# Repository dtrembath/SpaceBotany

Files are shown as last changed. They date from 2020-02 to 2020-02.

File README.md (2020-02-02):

# SpaceBotany
Details of aeroponic mister control using esp8266

This is supplementary material for the Amateur Professionals team entry in the Grow Beyond Earth contest (Feb 3, 2020). 
The design uses a 113kHz piezoelectric mister w/ WG3166A board to aeroponically grow lettuce plants.
See https://www.instructables.com/contest/beyondEarth/ for details.

Files in this repository inlude 'mister-esp8266-wiring.pdf', which shows the wiring for controlling the mister with an ESP8266 microcontroller. A DHT22 temp/humidity sensor is also included. 
Data is uploaded to https://thingspeak.com/channels/948030

The Arduino IDE is used to upload the 'space_botany_contest_mister.ino' code to an Adafruit Feather Huzzah ESP 8266.
You will also need to download the 'secrets.h' file into the same directory as 'space_botany_contest_mister.ino'.
Edit the information in 'secrets.h' to add your wifi and ThingSpeak credentials.

The 'esp8266-mister.fzz' file is included if you'd like to open it with the Fritzing software tool.

See https://learn.adafruit.com/adafruit-feather-huzzah-esp8266/power-management for various ways to provide power to the ESP8266.
The WG3166A mister board draws a fair amount of current, so it has its own 5v 1.5A power supply.

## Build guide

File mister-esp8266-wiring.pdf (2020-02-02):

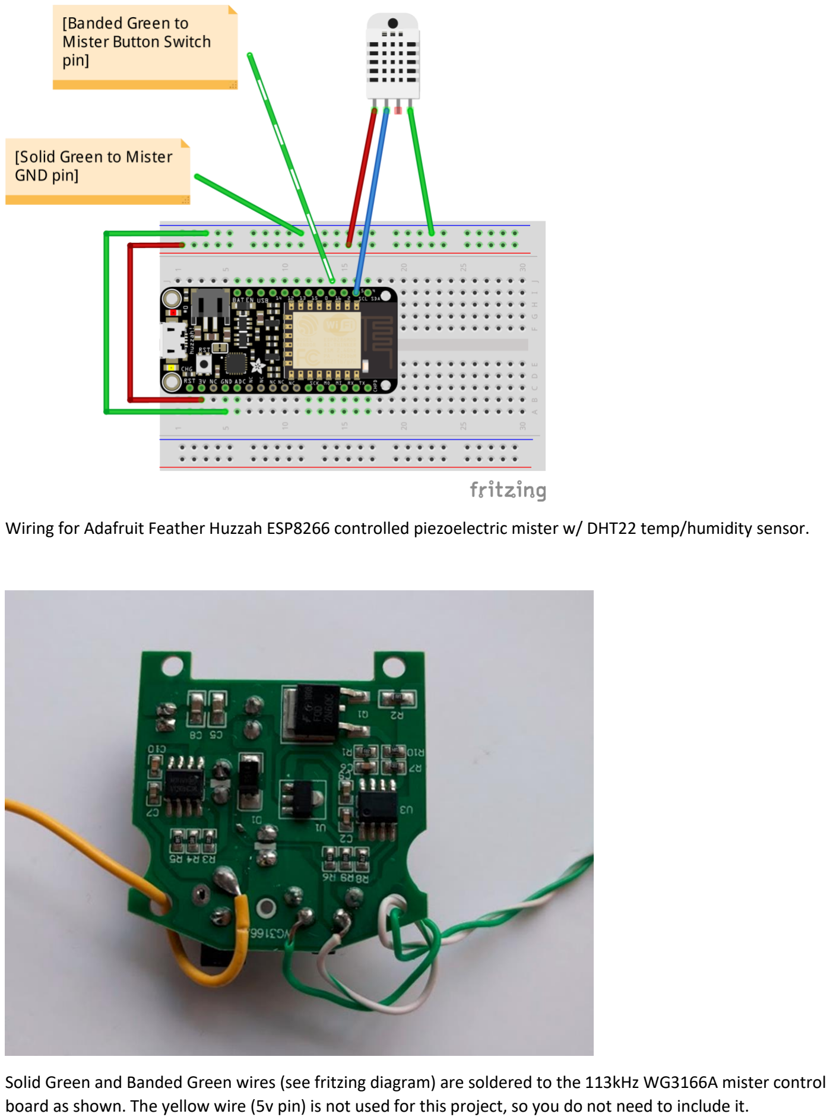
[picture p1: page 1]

Wiring for Adafruit Feather Huzzah ESP8266 controlled piezoelectric mister w/ DHT22 temp/humidity sensor.

Solid Green and Banded Green wires (see fritzing diagram) are soldered to the 113kHz WG3166A mister control board as shown. The yellow wire (5v pin) is not used for this project, so you do not need to include it.

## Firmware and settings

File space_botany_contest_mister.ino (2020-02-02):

// Code used for Space Botany mister experiments
// The ESP8266 uses the 'onTime' and 'offTime' you provide to control the WG3166A mister.
// Temperature and Humidity are recorded using a DHT22 sensor.
// 'onTime', 'offTime', temperature and humidity are sent via wifi to a ThingSpeak channel.
// See thingspeak.com to set up a free public channel to upload and view your data. 
 
// Hardware: Adafruit Feather Huzzah ESP8266, DHT22, 113kHz piezoelectric mister w/ WG3166A control board  
// Arduino IDE Board: Adafruit Feather HUZZAH ESP8266 

#include "secrets.h" // Note: edit this file to include your wifi & Thingspeak credentials
#include <DHT.h>  // library for DHT temp/humidity sensor

#include <ESP8266WiFi.h>

// This code allows you to specify in advance up to 5 known wifi locations. 
// If you only plan to use a single network, just add info for case 1.

// cycle through known possible ssid's (max 5)
void attemptToConnect(int current_connection_point) {
  switch (current_connection_point) {
    case 1:
      Serial.println("Connecting to ");
      Serial.println(SECRET_SSID_SSID1);
      WiFi.begin(SECRET_SSID_SSID1, SECRET_PASS_PASSWORD1);
      break;
    case 2:
      Serial.println("Connecting to ");
      Serial.println(SECRET_SSID_SSID2);
      WiFi.begin(SECRET_SSID_SSID2, SECRET_PASS_PASSWORD2);
      break;
    case 3:
      Serial.println("Connecting to ");
      Serial.println(SECRET_SSID_SSID3);
      WiFi.begin(SECRET_SSID_SSID3, SECRET_PASS_PASSWORD3); 
      break;
    case 4:
      Serial.println("Connecting to ");
      Serial.println(SECRET_SSID_SSID4);
      WiFi.begin(SECRET_SSID_SSID4, SECRET_PASS_PASSWORD4);
      break;
    case 5:
      Serial.println("Connecting to ");
      Serial.println(SECRET_SSID_SSID5);
      WiFi.begin(SECRET_SSID_SSID5, SECRET_PASS_PASSWORD5);
      break;  
    default:
      Serial.println("Connection credentials invalid for current integer ");
      Serial.println(current_connection_point);
      // default is optional
      break;
  }
  return;
}

String apiKey = SECRET_WRITE_APIKEY_CH;     //  API Write Key for your ThingSpeak channel
const char* server = "api.thingspeak.com";

#define DHTPIN01 5          // (Board Label 5, Pin 14, IDE 5 on esp8266 feather)
int misterPin = 16;       // (Board Label 16 on esp8266 feather)

DHT dht01(DHTPIN01, DHT22);

unsigned long currentTime;
unsigned long turnOnTime = 0;
unsigned long turnOffTime = 0;
// onTime & offTime can be changed to alter growing conditions
unsigned long onTime = 60000; // mister On for 1 min (60 sec)
unsigned long offTime = 3540000; // mister Off for 59 min (3540000sec)
// unsigned long onTime = 5000; // for debugging, mister On 5 sec
// unsigned long offTime = 15000;  // for debugging, mister Off for 15 sec

WiFiClient client;

void setup() {
  Serial.begin(115200);
  Serial.println();
  Serial.println("Running file 'nasa_misters_contest.ino'");
  delay(10);
  
  int connection_attempt = 0;
  int current_connection_point = 0;
  
// connect to wifi  
  while (WiFi.status() != WL_CONNECTED) {
    current_connection_point = 1;
    while (current_connection_point < 6) {
      attemptToConnect(current_connection_point);
      for (int i = 0; i <= 20; i++) {     // for debugging 10 sec is usually long enough to wait for a connection
        if (WiFi.status() != WL_CONNECTED) {
          delay(500);
          Serial.print(".");
        }
      }
      Serial.print("\n");
      if (WiFi.status() == WL_CONNECTED) {
        break;  
      }
      current_connection_point++;
    }   
    if (WiFi.status() != WL_CONNECTED) { 
      connection_attempt++;
      Serial.print("WiFi connection attempt failed ");
      Serial.print(connection_attempt); 
      Serial.println(" times.");
    }
  }
  Serial.println("");
  Serial.println("WiFi connected");

// test misterPin operation
  pinMode(misterPin, OUTPUT);
}


void loop() {
// set time for mister to be On and Off, in msec
// this involves setting a digital I/O pin high or low
// note that On is LOW, since the mister's onboard switch connects 2 GND points when pressed
  
  int misterOnOff = 1;  
  recordTempHumidity(misterOnOff);
  pressButton();
  turnMisterOn(onTime);
//  digitalWrite(misterPin, LOW);  // reset state of mister
  misterOnOff = 0;  
  recordTempHumidity(misterOnOff);
  pressButton();
  turnMisterOff(offTime);
//  digitalWrite(misterPin, HIGH);  // reset state of mister
}

// This is the only tricky part of using a microcontroller to control the mister.
// You need to digitally approximate a manual button press.
// If the delay is either too long or too short, the mister will consider the change as noise,
// rather than a button press, so a state change (ON/OFF or OFF/ON) will not occur. 

void pressButton() {
    digitalWrite(misterPin, LOW);
    delay(200);
    digitalWrite(misterPin, HIGH);
}

void turnMisterOn(unsigned long onTime) {
  currentTime = millis();
  turnOffTime = currentTime + onTime;
  Serial.print("Starting timer. Mister will stay on for ");
  Serial.print(onTime/1000); //prints time since program started
  Serial.println(" seconds.");
  Serial.print("Current time = ");
  Serial.println(currentTime);
  Serial.print("Turn off time = ");
  Serial.println(turnOffTime);
  while (currentTime < turnOffTime) {
    currentTime = millis();
    digitalWrite(misterPin, HIGH);
    delay(1000);
  }
  Serial.print("Current time = ");
  Serial.println(currentTime);
  Serial.print("Turn on time = ");
  Serial.println(turnOffTime);
  return;
}

void turnMisterOff(unsigned long offTime) {
  currentTime = millis();
  turnOnTime = currentTime + offTime;
  Serial.print("Stopping timer. Mister will stay off for ");
  Serial.print(offTime/1000); //prints time since program started
  Serial.println(" seconds.");
  Serial.print("Current time = ");
  Serial.println(currentTime);
  Serial.print("Turn on time = ");
  Serial.println(turnOnTime);
  while (currentTime < turnOnTime) {
    currentTime = millis();   
    digitalWrite(misterPin, HIGH);
    delay(1000);
  }
  Serial.print("Current time = ");
  Serial.println(currentTime);
  Serial.print("Turn on time = ");
  Serial.println(turnOnTime);
  return;
}

void recordTempHumidity(int misterOnOff) {
  dht01.begin();
  float temp1 = dht01.readTemperature();
  float hum1 = dht01.readHumidity();
      
  Serial.print("Temperature: ");
  Serial.print(temp1);
  Serial.println(" degrees C");
  Serial.print("Humidity: ");
  Serial.print(hum1);
  Serial.print(" %");
  Serial.println(); 

// don't make posting fail if sensor does not have a reading
  if (isnan(temp1)) {
     temp1 = -1;
  }
  
  if (isnan(hum1)) {
     hum1 = -1;
  }
                     
  if (client.connect(server,80)) {  //   "184.106.153.149" or api.thingspeak.com        
// create the string of data to post to thingspeak
    String postStr = apiKey;
    postStr +="&field1=";
    postStr += String(misterOnOff);
    postStr +="&field2=";
    postStr += String(1 - misterOnOff);
    postStr +="&field3=";
    postStr += String(temp1);
    postStr +="&field4=";
    postStr += String(hum1);
    postStr += "\r\n\r\n";

// post it    
    client.print("POST /update HTTP/1.1\n");
    client.print("Host: api.thingspeak.com\n");
    client.print("Connection: close\n");
    client.print("X-THINGSPEAKAPIKEY: "+apiKey+"\n");
    client.print("Content-Type: application/x-www-form-urlencoded\n");
    client.print("Content-Length: ");
    client.print(postStr.length());
    client.print("\n\n");
    client.print(postStr);
    
// tell the monitor what you posted
    Serial.print("Temperature: ");
    Serial.print(temp1);
    Serial.print(" degrees Celcius, Humidity: ");
    Serial.print(hum1);
    Serial.print(" %");
    Serial.println();
    Serial.println("Sent to Space Botany Channel.");
  }
  client.stop();
  Serial.println(" Waiting...");
  
}

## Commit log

2020-02-01 Added fritzing diagram to control WG3166A mister
    This uses the Adafruit Feather Huzzah ESP8266 to control the mister + a DHT22 temp/humidity sensor.
    [esp8266-mister.fzz]
2020-02-02 Add wiring of pins on WG3166A mister control board
2020-02-02 Add wiring diagram for WG3166A mister control
    Uses Adafruit Feather Huzzah ESP8266 to control WG3166A mister
2020-02-02 Add Arduino IDE files to control WG3166A mister
    The ESP8266 uses the Arduino IDE to run the code to control the mister
